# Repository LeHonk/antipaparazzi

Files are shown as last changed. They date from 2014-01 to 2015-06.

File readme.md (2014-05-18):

# Antipaparazzi device

This project is intended to be an anti-paparazzi device.
The idea is to detect if a camera system or other optical system is directed towards the device.
The detection is done by scanning the surroundings with a laser beam, and detect any reflections.
All optical systems will have a retro-reflex, directing the reflected beam in the opposing direction of the incoming beam, 
e.g. back to the device.

## Phased-Locked-Loop design

Natural speed of the combination of motor and drive wheel results in a scanning speed of 16 Hz.
Multiplied by 360 (for 1 degree of angular resolution) means that the clock should be around 5.8 kHz.

Choosing oscillator components according to HFE4046B datasheet section 11.1 (VCO without frequency offset)with a 5760 Hz f0 gives;
	R1 = 100 kOhm	or	R1 = 10 kOhm
	C1 = 800 pF		C1 = 7000 pF

With assumed limits of 12 to 20 Hz the clock limits become 4320 resp. 7200 Hz. (fmax/fmin = 1.667)
Choosing components (VFO with frequency offset) leads to values:
	R1 = 80 kOhm
	R2 = 100 kOhm
	C1 = 2000 pF

Components at hand:
	R1 = 10 kOhm
	C1 = 10 nF

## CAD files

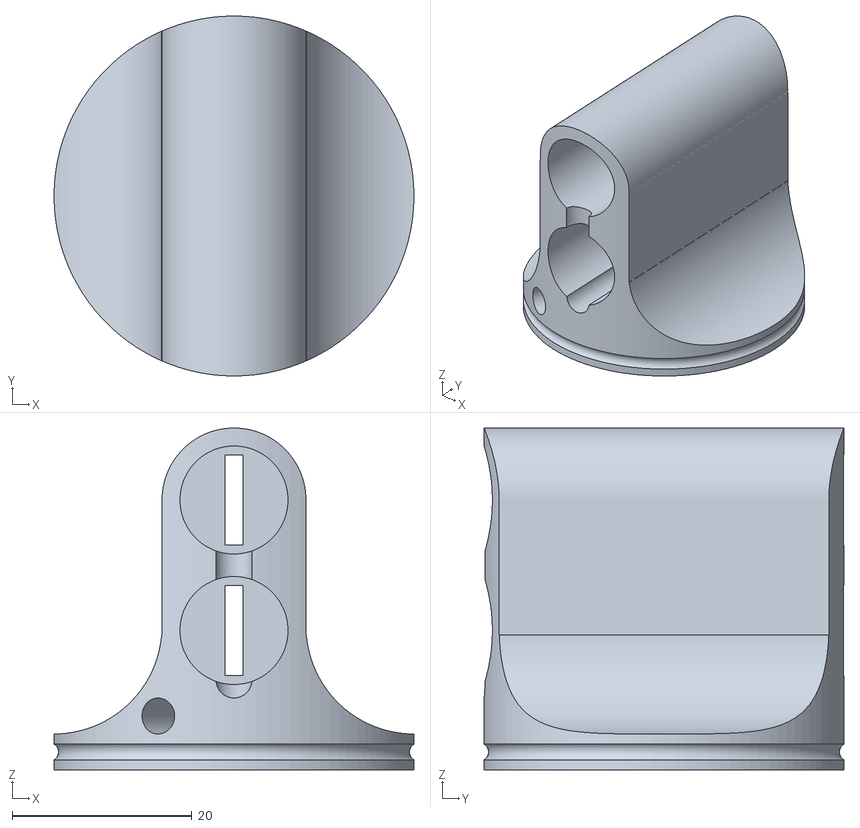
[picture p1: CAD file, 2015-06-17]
scanhead.stl
40.0 x 40.0 x 38.0

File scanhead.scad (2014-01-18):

$fn=100;

module slip_ring() {
	translate([0,0,-19]) cylinder(h=19, r=11);						// Main housing
	difference() {
		translate([0,0,-2.4]) cylinder(h=2.4, r=22);					// Flange
		for (t = [0,120,240]) {
			rotate([0,0,t]) translate([17.5,0,-2.5]) cylinder(h=2.6,r=2.75);	// Mounting holes
		}
	}
	cylinder(h=9,r=3.9);													// Rotor
}


difference() {
	render(convexity=10) intersection() {
		union() {
			translate([0,0,30]) rotate([90,0,0]) cylinder(h=40,r=8, center=true);	// Top
			translate([0,0,21.75]) cube([16,40,15.5], center=true);					// Main riser
			difference() {
				translate([0,0,7.25]) cube([40,40,15.5], center=true);					// Base
				translate([20,-1,16]) rotate([90,0,0]) cylinder(h=42, r=12, center=true);	// Rounding
				translate([-20,-1,16]) rotate([90,0,0]) cylinder(h=42, r=12, center=true);	// Rounding
			}
		}
		cylinder(h=40, r=20);											// Main house
	}
	cylinder(h=8, r=4);													// Rotor cavity
	cylinder(h=11,r=2);													// Cable riser
	translate([0,0,10])	rotate([90,0,0]) cylinder(h=21, r=2);		// Cable channel
	translate([0,-20,15.5]) cylinder(h=14.5, r=2);					// Cable channel between mounting
	translate([0,0,15.5]) rotate([90,0,0]) union() {				// Laser mounting
		cylinder(h=38,r=6, center=true);
		cylinder(h=20,r=6);
		cube(size=[2,10,41], center=true);
	}
	translate([0,0,30])	rotate([90,0,0]) union() {					// Detector mounting
		cylinder(h=38,r=6, center=true);
		cylinder(h=20,r=6);
		cube(size=[2,10,41], center=true);								// Apperture
	}
	translate([0,0,6])	rotate([0,90,245]) cylinder(h=21, r=2);	// Set Screw hole
	rotate_extrude(convexity=4) translate([20.5,2,0]) circle(1);	// Drive belt groove
}


// Slip ring
%translate([0,0,-1]) slip_ring();

// Top Hat
%translate([0,0,-133.4]){
	cylinder(h=130, r=90);
	translate([0,0,-10]) cylinder(h=10, r=160);
}

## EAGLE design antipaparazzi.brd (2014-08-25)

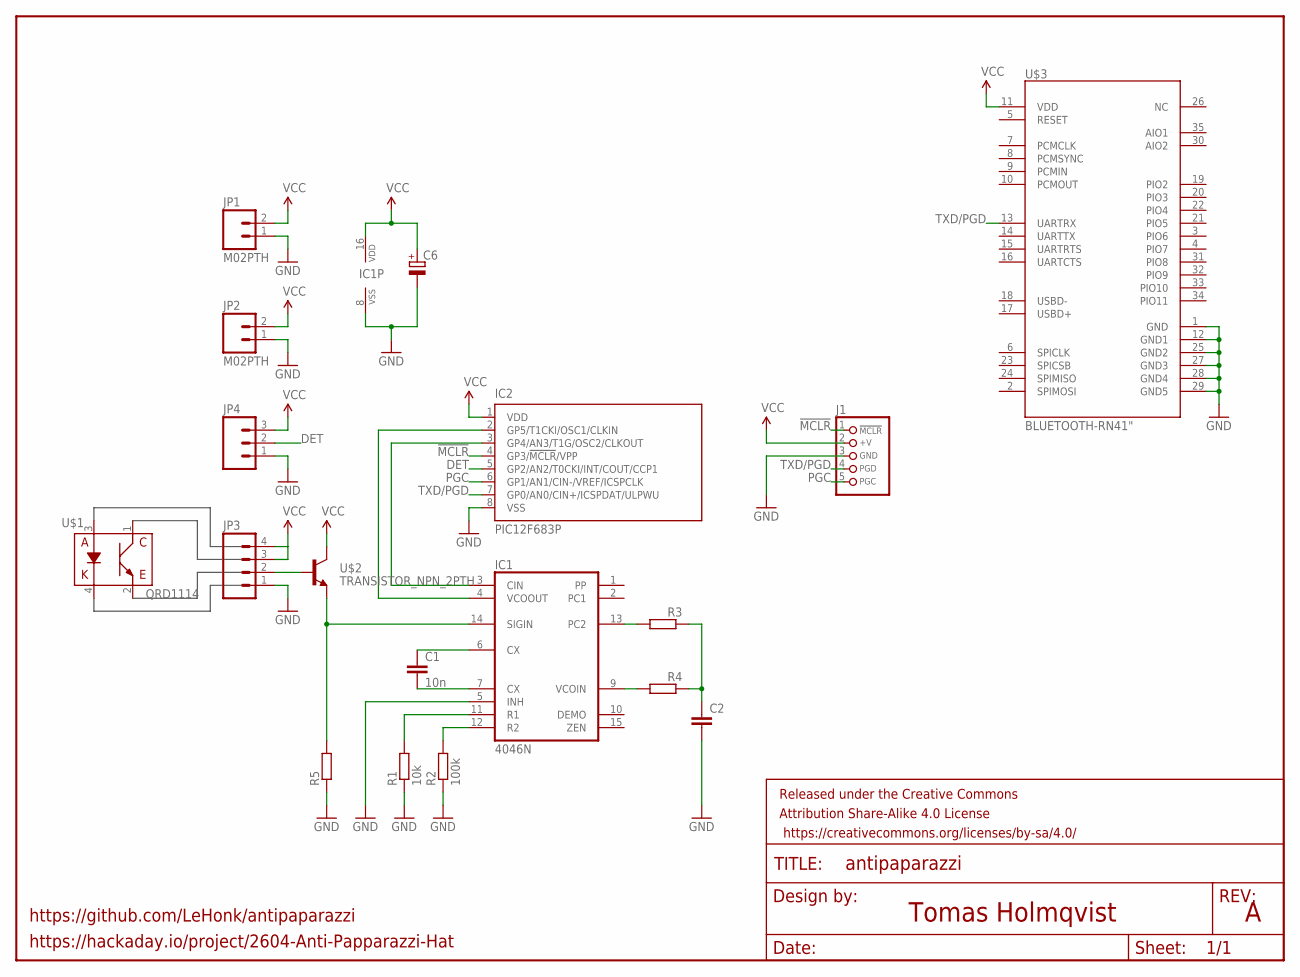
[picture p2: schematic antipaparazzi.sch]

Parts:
C1: 10n; C025_050-025X075
C2: C-EU025_050-025X075; C025_050-025X075
C6: CPOL-EUE2.5-6; E2,5-6
FRAME1: FRAME-LETTER; CREATIVE_COMMONS
IC1: 4046N; DIL16
IC2: PIC12F683P; DIL8
J1: CON_HEADER_PRG_PIC_ICSP0.1INCH_B; HEADER_PRG_1X05_ICSP_B
JP1, JP2: M02PTH; 1X02
JP3: M04PTH; 1X04
JP4: M03PTH; 1X03
R1: 10k; 0207/2V
R2: 100k; 0207/2V
R3, R4, R5: R-EU_0207/2V; 0207/2V
U$1: QRD1114
U$2: TRANSISTOR_NPN_2PTH; TO-92
U$3: BLUETOOTH-RN41"; RN41

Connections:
!MCLR: IC2.4 (GP3/!MCLR!/VPP), J1.1 (/MCLR)
DET: IC2.5 (GP2/AN2/T0CKI/INT/COUT/CCP1), JP4.2
GND: C2.2, C6.-, IC1.5 (INH), IC1.8 (VSS), IC2.8 (VSS), J1.3 (GND), JP1.1, JP2.1, JP3.1, JP4.1, R1.1, R2.1, R5.1, U$3.1 (GND), U$3.12 (GND1), U$3.25 (GND2), U$3.27 (GND3), U$3.28 (GND4), U$3.29 (GND5)
unnamed: IC1.4 (VCOOUT), IC2.2 (GP5/T1CKI/OSC1/CLKIN)
unnamed: IC1.3 (CIN), IC2.3 (GP4/AN3/T1G/OSC2/CLKOUT)
unnamed: C1.1, IC1.6 (CX)
unnamed: C1.2, IC1.7 (CX)
unnamed: IC1.12 (R2), R2.2
unnamed: IC1.11 (R1), R1.2
unnamed: IC1.14 (SIGIN), R5.2, U$2.3 (E)
unnamed: C2.1, R3.1, R4.1
unnamed: IC1.13 (PC2), R3.2
unnamed: IC1.9 (VCOIN), R4.2
unnamed: JP3.2, U$2.2 (B)
PGC: IC2.6 (GP1/AN1/CIN-/VREF/ICSPCLK), J1.5 (PGC)
TXD/PGD: IC2.7 (GP0/AN0/CIN+/ICSPDAT/ULPWU), J1.4 (PGD), U$3.13 (UARTRX)
VCC: C6.+, IC1.16 (VDD), IC2.1 (VDD), J1.2 (+V), JP1.2, JP2.2, JP3.3, JP3.4, JP4.3, U$2.1 (C), U$3.11 (VDD)

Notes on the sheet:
Tomas Holmqvist
https://hackaday.io/project/2604-Anti-Papparazzi-Hat
https://github.com/LeHonk/antipaparazzi

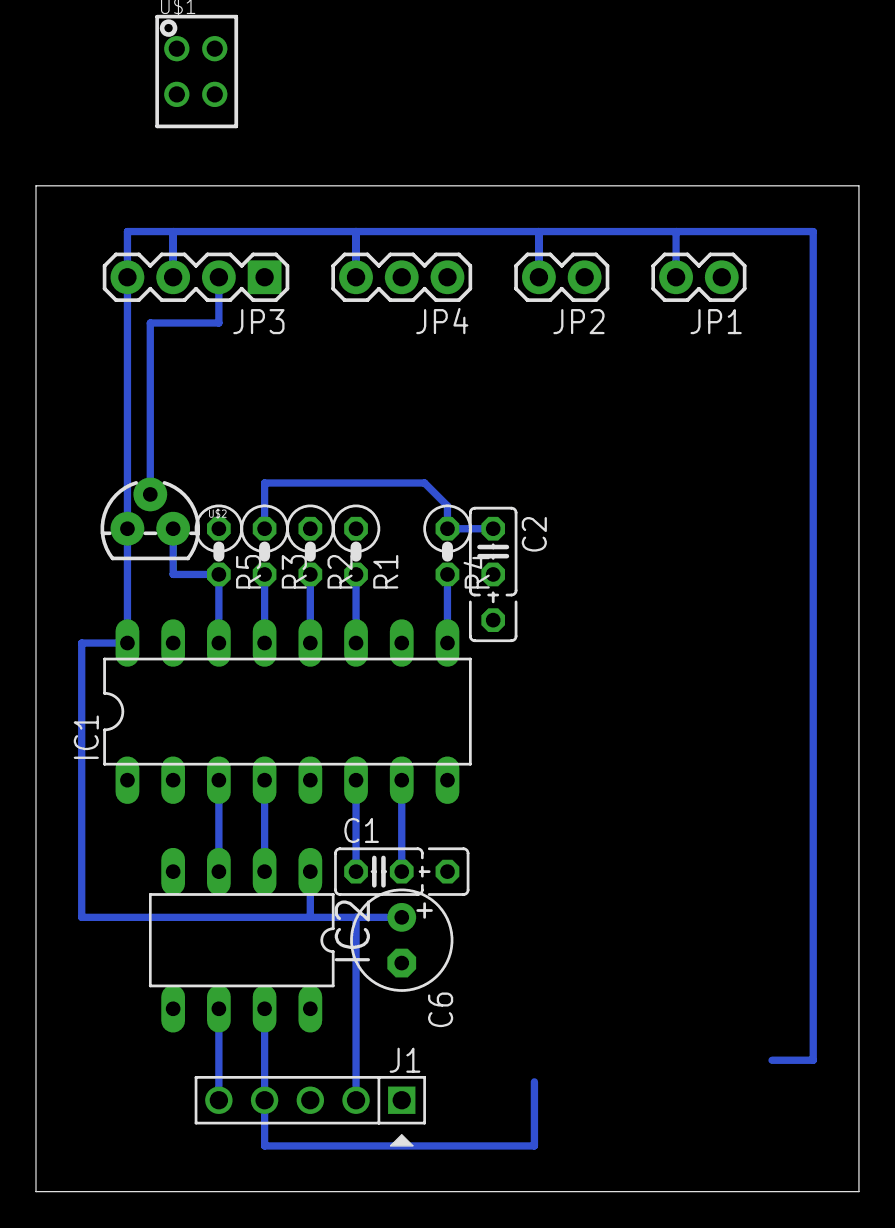
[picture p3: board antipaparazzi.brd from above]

Board: 2 copper layers, 45.7 x 55.9 mm, 19 parts (1 on the bottom side), 17 nets.

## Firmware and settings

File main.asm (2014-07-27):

	TITLE		"Antipaparazzi"
;=====================================================================================
;
;      Filename:  main.asm
;
;   Description:  Antipaparazzi Device Main file
;
;       Version:  1.0
;       Created:  14-01-19 12:57
;      Revision:  none
;      Compiler:  gputils
;
;        Author:  Tomas Holmqvist (TH), tomhol@gmail.com
;  Organization:  
;
;=====================================================================================

; TODO
;	* Use watchdog to enable laser
;	* Wrap-safe timer read
;	* Better detection

	PROCESSOR	12F683

	INCLUDE		"p12f683.inc"

TMR1_LOAD	EQU	(0xFFFF-360+1)	; Start counting on 360 less then max, 
					; ie overflow and generate timer 
					; interrupt after 360 counts

UART_DELAY	EQU	45		; Baud delay @ 8MHz ((8000000/4/9600-10)/3)=66

	UDATA_SHR
int_w		RES	1 		; Context save of w during interrupt
int_status	RES	1		; Context save of status during interrupt
putch_c		RES	1		; Char to transmit
putch_cnt	RES	1		; Bit loop counter
delay_cnt	RES	1		; Delay counter0

	__CONFIG _FCMEN_ON & _IESO_ON & _BOD_ON & _CPD_OFF & _CP_OFF & _MCLRE_ON & _PWRTE_ON & _WDT_OFF & _INTOSCIO

reset_vec	CODE	0x00
	goto	start

;===  FUNCTION  ======================================================================
; Name:  int_handler
; Description:  Handle various interrupts
;=====================================================================================
int_vec		CODE	0x04
int_handler:
	bsf	GPIO, GP4		; Erliest possible rise of puls out
	bcf	PIR1, CCP1IF		; Reenable Timer1 interrupt
	clrwdt				; Clear watchdog timer
	bcf	GPIO, GP4		; fall of puls out, not time critical
	retfie

;===  FUNCTION  ======================================================================
; Name:  putch
; Description:  Bitbanged uart transmit
; Note:         Destroys carry and W
;=====================================================================================
	GLOBAL	putch
putch:
	movwf	putch_c
	movlw	9			; 1 start bit + 8 bit + 1 stop bit
	movwf	putch_cnt
	bsf	STATUS, C		; Stop bit high at nineth iteration
	bcf	GPIO, GP0		; Start bit
	
putch_loop:				;				Acc'd cycles
	movlw	UART_DELAY		; Uart bit delay		1
	movwf	delay_cnt		;				2
bit_delay:
	decfsz	delay_cnt, f		;				(1)
	goto	bit_delay		; loop to previous instruction	(3)

	rrf	putch_c, f		; Rotate bit into carry		3
	btfsc	STATUS, C		;				4
	bsf	GPIO, GP0		; Carry set -> output high	5
	btfss	STATUS, C		;				6
	bcf	GPIO, GP0		; Carry clear -> output low	7
	decfsz	putch_cnt, f		;				8
	goto	putch_loop		; loop over all 8 (+1) bits	10

	movlw	UART_DELAY		; Uart bit delay		1
	movwf	delay_cnt		;				2
stopbit_delay:
	decfsz	delay_cnt, f		;				(1)
	goto	stopbit_delay		; loop to previous instruction	(3)
	goto	$+1			;				4
	goto	$+1			;				6
	goto	$+1			;				8
	return				;				10

start:
	BANKSEL	OSCCON
	movlw	71h
	movwf	OSCCON			; Internal 8Mhz system clock
	BANKSEL	GPIO
	movlw	B'00010001'		; GP0 (TxD), GP4 (Comp_In) High
	movwf	GPIO			; Clear all pins, except GP0 & GP4
	movlw	B'00000111'
	movwf	CMCON0			; No comparator used
	BANKSEL	ANSEL
	clrf	ANSEL			; All pins digital IO
	movlw	B'00101110'
	movwf	TRISIO			; GP5 in, GP4 out, GP3 nc, GP2 in, GP1 nc, GP0 out
	BANKSEL	T1CON
	movlw	B'00000011'
	movwf	T1CON			; Synchronous external clock source
	clrf	TMR1H			; Preload Timer1 counter
	clrf	TMR1L
	clrf	CCP1CON			; Turn off CCP to clear prescalers
	movlw	B'00001011'
	movwf	CCP1CON			; Compare mode, clear timer1
	movlw	low(D'360')		; Set up compare to generate 360 counts per revolution
	movwf	CCPR1L
	movlw	high(D'360')
	movwf	CCPR1H
	clrf	PIR1			; Clear all interrupt flags
	clrf	INTCON
	BANKSEL	PIE1
	bsf	IOC, IOC2		; Let detection pin trigger IOC flag => pulse elongation
	bsf	PIE1, CCP1IE		; CCP interrupt enable
	bsf	INTCON, PEIE		; Peripheral interrupt enable
	bsf	INTCON, GIE		; Global interrupt enable
	BANKSEL	T1CON
	bsf	T1CON, TMR1ON		; Start Timer1

main_loop:

check_detection:
	btfss	INTCON, GPIF		; poll detection sensor
	goto	main_loop		; Wait 4 next detection
detect:
	movf	TMR1L, w
	call	putch
	movf	TMR1H, w
	call	putch
wait_clear:
	btfsc	GPIO, GP2		; Wait for detection unassertion
	goto	wait_clear
	bcf	INTCON, GPIF		; Clear iterrupt flag
	goto	main_loop		; Wait 4 next detection
	
	END

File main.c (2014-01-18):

/*
 * =====================================================================================
 *
 *       Filename:  main.c
 *
 *    Description:  Antipaparazzi Device Main file
 *
 *        Version:  1.0
 *        Created:  14-01-02 12:57
 *       Revision:  none
 *       Compiler:  xc8
 *
 *         Author:  Tomas Holmqvist (TH), tomhol@gmail.com
 *   Organization:  
 *
 * =====================================================================================
 */
#include <xc.h>
#include <stdlib.h>
#include <stdio.h>
#include <stdint.h>

#pragma config CPD=OFF, CP=OFF, FCMEN=ON, IESO=ON, BOREN=ON, MCLRE=ON, PWRTE=ON, FOSC=INTOSCIO

#define	TMR1_LOAD (UINT16_MAX-360 + 1)		/* Start counting on 360 less then max, 
						   ie overflow and generate timer 
						   interrupt after 360 counts */

#define TXpin   GP0                             /* Sowrtware UART transmit pin */
#define UART_delay()    _delay(208)             /* Baud delay @ 8MHz */
/* 
 * ===  FUNCTION  ======================================================================
 *         Name:  int_handler
 *  Description:  Hadndle various interrupts
 * =====================================================================================
 */
void interrupt int_handler( void ) {
    if (TMR1IF) {
	TMR1 = TMR1_LOAD;
	GP4 = 1;                                /* Generate a pulse on GP4 */
	GP4 = 0;
	TMR1IF = 0;                             /* Reenable Timer1 interrupt */
    }
}		/* -----  end of static function t1  ----- */


/* 
 * ===  FUNCTION  ======================================================================
 *         Name:  putch
 *  Description:  Bitbanged uart transmit
 * =====================================================================================
 */
void putch( char c ) {
    uint8_t cnt = 8;
    TXpin = 0;                                  /* Start bit */
    UART_delay();
    while (cnt--) {
	TXpin = (c & 0x01);
	UART_delay();
	c>>=1;
    }
    TXpin = 1;                                  /* Stop bit */
    UART_delay();
}		/* -----  end of function putch  ----- */

void main(void) {
    OSCCON = 0xF0;				/* Internal 8Mhz system clock */
    T1CON = 0x6;                                /* Asynchronous external clock source */
    TMR1 = TMR1_LOAD;                           /* Preload Timer1 counter */
    CCP1CON = 0x05;				/* Capture mode, every rising edge */
    GPIO = 0x00;                                /* Clear all pins */
    TRISIO = ~0x10;                             /* GP4 Output */
    ANSEL = 0x00;                               /* All pins digital IO */
    CMCON0 = 0x07;				/* All pins digital IO */
    TMR1IF = 0;                                 /* Clear Timer1 interrupt flag */
    CCP1IF = 0;                                 /* Clear CCP Interrupt flag */
    TMR1IE = 1;                                 /* Timer1 interrupt enable */
    PEIE = 1;                                   /* Peripheral interrupt enable */
    GIE = 1;                                    /* Global interrupt enable */
    TMR1ON = 1;                                 /* Start Timer1 */
    while(1) {                                  /* Loop 4-evva */
    	if (CCP1IF) {                           /* Poll CCP interrupt flag */
            printf("%d\n", CCPR1 - TMR1_LOAD);  /* Print detected angle on stdout */
	    CCP1IF = 0;                         /* Reenable CCP "Interrupt" */
	}
    }
}

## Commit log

2008-01-01 Added scan head design
    [scanhead.scad]
2014-01-02 1:st Working revision
    Added MCRL release on install
    Enabled interrupts
2014-01-04 Added detection
    Detection via polled interruptflag.
    Detection reported via software bit-banged uart @ 9600 baud
2014-01-13 Added .stl to ignore-file
2014-01-14 Minor tweaks
    [scanhead.scad]
2014-01-15 Added extra cable channel
    Moved set screw hole out of belt drive groove.
    Edited some comments
    [scanhead.scad]
2014-01-18 Minor edits
    [scanhead.scad]
2014-01-21 Reimplemented in asm for faster interrupt response
2014-05-18 Functioning bitbang uart
2014-05-27 No interrupt execution, why?
2014-05-27 Switched to gputils toolchain
2014-07-23 Working interrupts, yheay.
    Damn you bankselect.
2014-07-27 Working
    But; small detection pulses on GP2 are missed by IOC system (polled at Q3)
    [main.asm]
2014-08-25 Added schematic and board
    In an initial rendering of whats on the breadboard
    Component values TBD.
    [antipaparazzi.brd, antipaparazzi.sch]
2015-06-17 Added stl generation and file
    [scanhead.stl]

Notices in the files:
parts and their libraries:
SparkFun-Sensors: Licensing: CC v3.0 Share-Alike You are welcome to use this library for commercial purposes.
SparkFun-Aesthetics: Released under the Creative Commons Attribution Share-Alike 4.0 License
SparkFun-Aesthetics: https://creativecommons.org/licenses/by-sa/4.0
